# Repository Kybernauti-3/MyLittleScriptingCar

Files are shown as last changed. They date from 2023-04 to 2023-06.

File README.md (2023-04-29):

# MyLittleScriptingCar
This is my little scripting car (Maybe autonomous in the future)

## Sources

These are the components (and their 3D models) I'm going to use in this projekt:
| Part | Component | Store page | 3D model |
| --- | --- | --- | --- |
| Brain (CPU) | Raspberry pi zero 2 w | [RPishop - Zero 2 w](https://rpishop.cz/zero/4311-raspberry-pi-zero-2-w-5056561800004.html) | [GrabCAD - Zero 2 w](https://grabcad.com/library/raspberry-pi-zero-2-w-1) |
| Camera | Raspberry Pi NoIR kamera V2 | [RPishop - NoIR v2](https://rpishop.cz/mipi-kamerove-moduly/331-raspberry-pi-noir-kamera-modul-v2.html) | [Thingiverse - Rpi Camera v2.1](https://www.thingiverse.com/thing:2376448/files) |
| Stepper motors + drivers | 2x 28BYJ-48 + ULN2003 | [Techfun - 28BYJ-48 + ULN2003](https://techfun.sk/produkt/krokovy-motor-28byj-48-modul-uln2003/)| [GrabCAD - 28BYJ-48 + ULN2003](https://grabcad.com/library/28byj-48-stepper-motor-and-uln2003-stepper-motor-driver-board-1) |
| Servo (180°) | Tower Pro 180° MG90S | [LaskaKit - Tower Pro MG90S](https://www.laskakit.cz/mini-servo-mg90s-s-kovovymi-prevody/) | [Thingiverse - MG90S Tower Pro](https://www.thingiverse.com/thing:253557/files) |
| Ultrasonic sensor | HY-SRF05 US sensor | [Dratek - HY-SRF05](https://dratek.cz/arduino/1735-meric-vzdalenosti-ultrazvukovy-5pin-hy-srf05-pro-arduino.html) | [Thingiverse - HY-SRF05](https://www.thingiverse.com/thing:2403007) |
| Main board (Arduino) | Arduino Nano (china clone) | [LaskaKit - Robotdyn Nano V3](https://www.laskakit.cz/robotdyn-arduino-nano-r3--atmega328p--pripajene-piny/) | [GrabCAD - Arduino nano](https://grabcad.com/library/arduino-nano-ch340-2) <br> _Not exactly the one I used..._ |
| Arduino terminal shield | Arduino Nano Terminal | [Techfun - Nano terminal](https://techfun.sk/produkt/arduino-nano-terminal-shield/) | [GrabCAD - Nano Terminal](https://grabcad.com/library/arduino-nano-expansion-board-1) |
| Logic converter | Bi-directional logic converter | [Techfun - I2C logic converter](https://techfun.sk/cs/produkt/i2c-logick%C3%BD-konverter-5v-3-3v-4-kan%C3%A1lov%C3%BD/) | [GrabCAD - logic converter](https://grabcad.com/library/logic-level-converter-5v-to-3-3v-module-1) |
| Charger + Potection | TP4056 Micro USB | [Dratek - TP4056 Micro USB](https://dratek.cz/arduino/971-micro-usb-nabijecka-baterii.html) | [GrabCAD - TP4056 Micro USB](https://grabcad.com/library/tp4056-cargador-de-baterias-litio-lipo-5v-1a-1) |
| Battery holder | 18650 Li-Ion Holder | [Techfun - 18650 Holder](https://techfun.sk/cs/produkt/drz%C3%A1k-pro-jednu-18650-li-ion-baterii/) | [GrabCAD - 18650 Holder](https://grabcad.com/library/18650-battery-holder-generic-1) |
| Step-up converter | M 407 s MT3608 | [RadioKus - M 407](https://www.radiokus.cz/m-407-napajeci-modul-step-up-menic-2a-s-mt3608) | []() |
| Battery | 18650 Li-Ion 2800mAh 10A | [Techfun - 18650 2800mAh](https://techfun.sk/cs/produkt/18650-baterie-tenpower-inr18650-22he-2800mah-10a/) | []() |

TODO:

- [x] Gather all sources
- [x] Design chassis
- [x] Print and ready the chassis
- [x] Complete the hardware
- [x] Write the software
- [ ] Write the framework
- [ ] Add some use for the camera
- [ ] Finalize
- [ ] Play with it :)

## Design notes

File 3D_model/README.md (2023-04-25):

# 3D model for the car

This is a folder with images of all 3D models.

The parts were made (and are stored) in
[onShape](https://www.onshape.com/en/).

-----------------------------------------------------------

## Latest update:

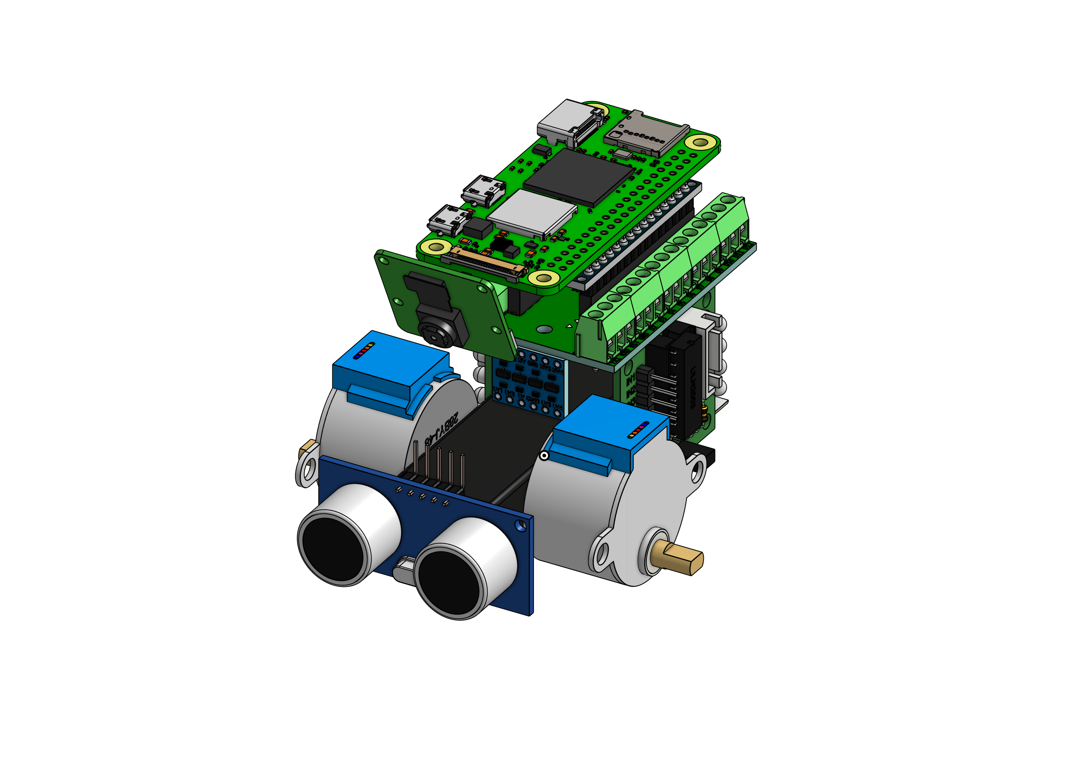
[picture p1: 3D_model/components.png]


Imported all the current parts. This is a visualization of how the parts will be placed in the final case.

> Actually made it completely different...

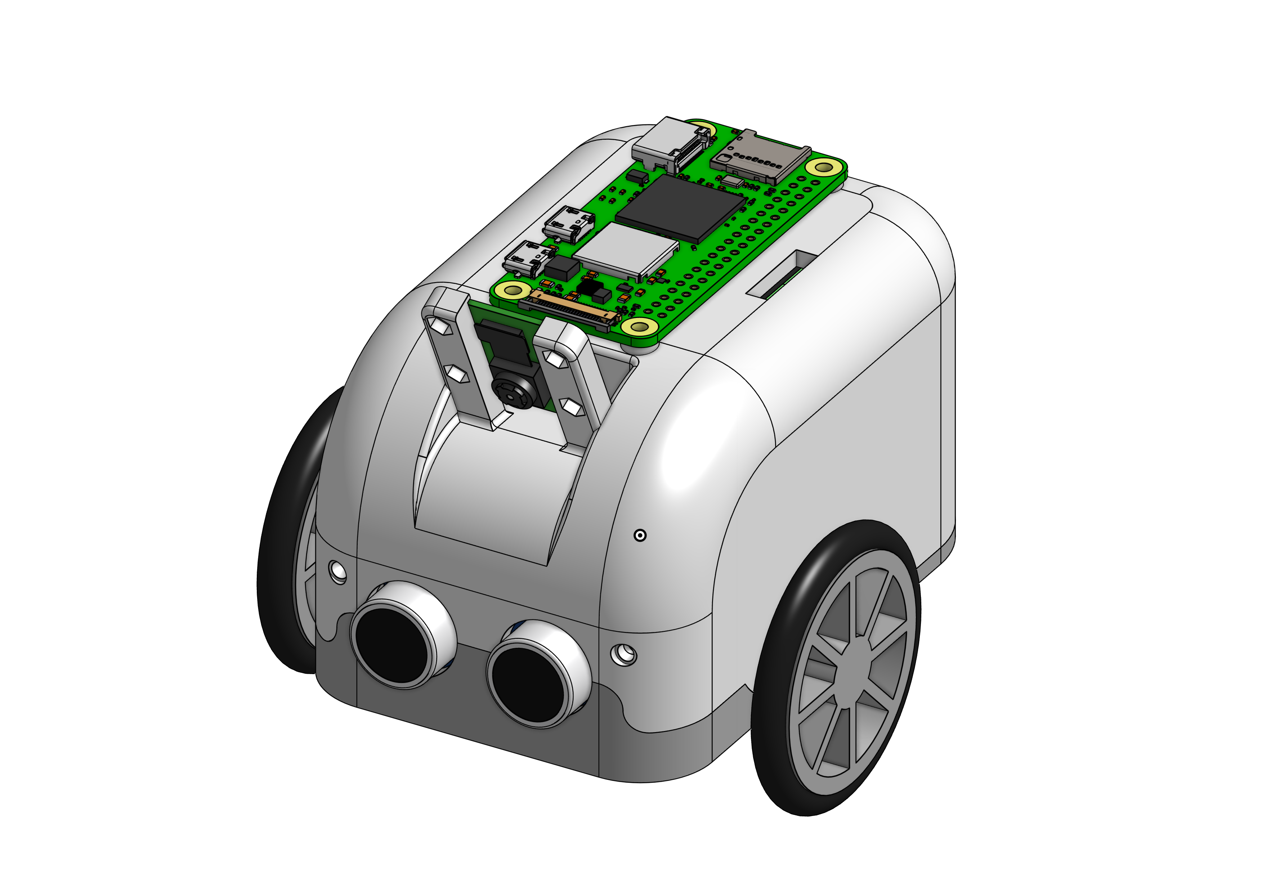
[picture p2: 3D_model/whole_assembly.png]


This is the whole assembly: All components + created parts

-----------------------------------------------------------

*The whole model can be found on the onShape cloud: [MyLittleScriptingCar](https://cad.onshape.com/documents/853826ab736a7e89ca60314d/w/e4e5486c53d8f1f4ba14f67f/e/c2fb18a20a1dab14190ffd40)*

*The model is also under HUGE development and I just don't want to spend that much time just exporting and copying files.*

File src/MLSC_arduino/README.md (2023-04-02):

# MyLittleScriptingCar _– Arduino part_

This is part of my project, that is dedicated to arduino.
For now, it contains [main.cpp](./src/main.cpp) and my custom library for controlling stepper motors – [EightStepMotor](./lib/EightStepMotor/)

In the future, this will contain all the code, that will be uploaded on the arduino, which means UART comunication, Ultrasonic senzor and maybe IMU and servo, but I'll might leave those out...

Also, there's a dependency in [platformio.ini](./platformio.ini) on Arduino Stepper library, but I used that library just as a reference, so it will get deleted later.

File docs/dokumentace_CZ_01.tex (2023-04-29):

\documentclass[12pt]{article}
\usepackage{blindtext}
\usepackage{geometry}
\geometry{
	a4paper,
	left=40mm,
	right=15mm,
	top=30mm,
	bottom=35mm,
 }
\usepackage{setspace}
% Seznam balíků
\usepackage{comment}
\usepackage{lmodern}
\usepackage{cmap}
\usepackage[czech]{babel}
\usepackage[T1]{fontenc}
\usepackage[utf8]{inputenc}
\usepackage{graphicx}
\usepackage{epstopdf}
\usepackage{makeidx}
\usepackage{listings}
\usepackage[export]{adjustbox}
\usepackage[font=scriptsize,labelfont=bf]{caption}
\usepackage{booktabs}
\usepackage{subcaption}
\usepackage{array}
\usepackage{multirow}
\usepackage{tabularray}
\usepackage{enumitem}
\usepackage{tocbibind}
\usepackage{courier}
\usepackage{pdfpages}
\usepackage{float}
\usepackage{hyperref}
\hypersetup{
	colorlinks,
	citecolor=black,
	filecolor=black,
	linkcolor=black,
	urlcolor=black
}
\usepackage{times}
\graphicspath{{./images/}}

% Začátek dokumentu
\begin{document}
	% Titulní stránka
	\begin{titlepage}
		\centering
		\fontfamily{lmss}\selectfont
		\begin{tabular}{m{0.2\linewidth}m{0.8\linewidth}}
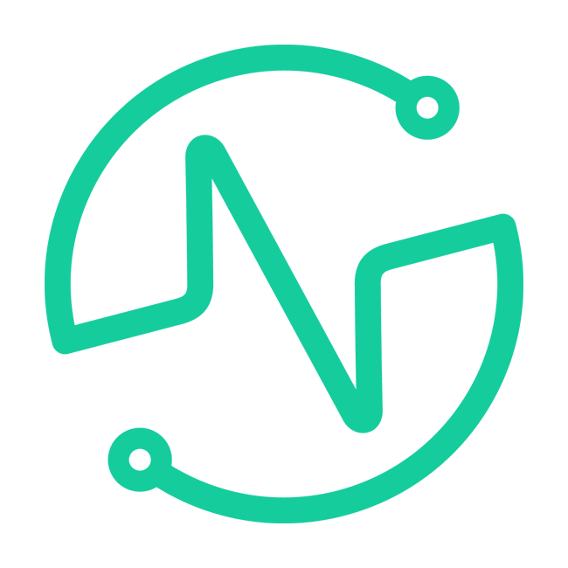
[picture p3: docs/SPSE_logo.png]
			
			&\centering
			\textbf{Vyšší odborná škola}\par
			\textbf{a Střední průmyslová škola elektrotechnická}\par
			\textbf{Plzeň, Koterovská 85}
		\end{tabular}
		\centering
		\vfill
		{\Huge\sc\textsf{\textbf{Ročníková práce}}\par}
		\raggedright
		\vspace{4cm}
		{\Large Téma: \textbf{Programovatelné auto}\par}
		\vfill
		
		% Spodní část titulní stránky
		\textbf{\begin{tabular}{ll}
			Autor práce:		&	Jan Ocelík \\
			Obor studia:		&	78-42-M/01 Technické lyceum \\
			Třída:				&	3. L \\
			Předmět:			&	Kybernetika \\
			Zadávající učitel:	&	Jiří Švihla \\
			Dne:				&	28. 4. 2023 \\
								&	\\
			Hodnocení:			&	\\
		\end{tabular}}
	\end{titlepage}

	% Zadání
	\thispagestyle{empty}
	\includepdfset{offset=15mm 0mm,noautoscale,pages={-},pagecommand={}}
	\includepdf[pages=1]{Zadani_RP_TL_22_23.pdf}
	
	\begin{spacing}{1.5}
	
	% Anotace
	\newpage
	\thispagestyle{empty}
	\section*{Anotace}
	\addcontentsline{toc}{section}{Anotace}
	\paragraph{} Cílem této ročníkové práce je za pomoci opensource programů navrhnout a z opensource komponent poskládat robotické autíčko pro začátečníky i pokročilé s možností jednoduchého sestavení. Dalším úkolem je vyvinout firmware a API pro jednoduché skriptové programovaní i komplexnější programování s využitím obrazového vstupu. Dalším úkolem je připravit ukázkové příklady kódu k předvedení jednotlivých funkcí robota. Posledním úkolem je zpříjemnit práci s robotem, zhodnotit přínosy a možnosti využití projektu ve vzdělávání a vypracovat potřebnou dokumentaci.
	\vfill
	\paragraph{} „Prohlašuji, že jsem tuto práci vypracoval samostatně a použil literárních pramenů a informací, které cituji a uvádím v seznamu použité literatury a zdrojů informací.“
	\paragraph{} „Souhlasím s využitím mé práce učiteli VOŠ a SPŠE Plzeň k výuce.“
	\paragraph{} \hfill Plzni dne: .................... Podpis: ....................
	
	% Poděkování
	\newpage
	\thispagestyle{empty}
	\section*{Poděkování}
	\addcontentsline{toc}{section}{Poděkování}
	\paragraph{} Tímto bych chtěl poděkovat vedoucímu práce Jiřímu Švihlovi za pomoc s výběrem komponent a obsahem dokumentace a rodině a přátelům za psychickou podporu. Také děkuji všem dohromady za to, že mě k tomu včas dokopali.
	
	% Obsah
	\newpage
	\tableofcontents
	
	% Úvod
	\newpage
	\section{Úvod}
	\paragraph{} V dnešní době se stále více hovoří o automatizaci a digitalizaci a tyto trendy mají velký vliv na společnost. Robotika a autonomní systémy jsou jednou z klíčových oblastí, které se rozvíjejí v rámci těchto trendů a mají potenciál změnit mnoho aspektů našeho života.
	\paragraph{} Vzdělávání a výuka v této oblasti se také stávají stále důležitějšími, protože mnoho pracovních pozic, které budou v budoucnosti vyžadovat znalosti robotiky a programování, ještě neexistuje. Výuka v této oblasti tak může být klíčová pro přípravu studentů na pracovní trh budoucnosti.
	\paragraph{} Proto jsem se rozhodl věnovat svou ročníkovou práci právě problematice robotiky a vytvořit autonomní auto, které bude sloužit jako výuková pomůcka. Můj záměr je ukázat, jak moderní technologie mohou být využity k tomu, aby byli studenti lépe připraveni na budoucí výzvy v oblasti robotiky a informatiky.
	\paragraph{} Při tvorbě prototypu se budu snažit využít nejnovější poznatky v oblasti robotiky a programování, a to jak z teoretického hlediska, tak praktických zkušeností z mých předchozích aktivit. Cílem bude vytvořit zařízení, které bude snadno ovladatelné a srozumitelné pro studenty různých věkových kategorií, a zároveň bude dostatečně funkční a výkonné pro splnění zadaných úkolů.
	\paragraph{} Věřím, že tato ročníková práce přispěje k popularizaci robotiky a podpoří zájem studentů o tuto oblast. To může mít pozitivní vliv na jejich budoucí kariéru a na rozvoj robotiky v České republice.
	
	% Cíle a požadavky
	\newpage
	\subsection{Cíle a požadavky}
	
	\subsubsection{Komponenty (moduly)}
	\paragraph{} Hlavním cílem této ročníkové práce je návrh a výroba robota z běžně dostupných materiálů, v tomto případě ze snadno sehnatelných modulů.
	\paragraph{} Moduly by měly být zároveň opensource, aby si software pro ně mohl programovat každý, který se k robotovi dostane, nebo si ho sám vyrobí.
	\paragraph{} Důležitý je také výběr napájení, v případě robotického auta tedy baterie, tak, aby udrželo robota v provozu po přiměřeně dlouhou dobu a aby zároveň dokázalo vykrýt proudové špičky.
	
	\subsubsection{Šasi (tělo)}
	\paragraph{} Tělo robota by mělo být vyrobeno tak, aby bylo plně uzavíratelné, tedy bezpečné pro jakýkoli přenos i při nešetrném zacházení, ale aby se dal robot také provozovat s plně přístupnými veškerými propojkami a bylo tedy snadné ladit jeho software za provozu.
	
	\subsubsection{API}
	\paragraph{} Jedním z dalších požadavků je co nejvíce zpříjemnit uživateli práci s robotickým autem, tedy vytvořit nějaké API nebo knihovnu.
	\paragraph{} Nedílnou součástí je také dokumentace k danému API/knihovně a to proto, aby si i nový uživatel zvládl bez jakékoli pomoci robota pomocí daného API/knihovny naprogramovat.
	
	% Návrhový software
	\newpage
	\subsection{Návrhový software}
	
	\subsubsection{Onshape}
	\paragraph{} Onshape je online software pro návrh 3D součástí. V programu se vytváří takzvaný dokument, ve kterém se nadále dají zakládat \uv{studia}. Onshape nabízí mnoho zajímavých možností, běžného uživatele však zajímají tato tři hlavní studia - \textbf{Part Studio}, \textbf{Assembly} a \textbf{Drawing}.
	\subsubsection*{Part Studio}
	\paragraph{} Part Studio slouží, jak už název napovídá, k vytváření jednotlivých dílů. Díly se vytvářejí a upravují pomocí příkazů, jako například \textbf{Sketch} (sloužící k sestrojení 2D náčrtu), \textbf{Extrude} (\uv{vytáhnutí} náčrtu do třetího rozměru) nebo \textbf{Fillet} (zaoblení hran). Tyto příkazy lze vyvolat kliknutím na jejich ikonu v horní liště programu, přepsáním jejich názvu do \textbf{Search tools}, nebo, u některých více používaných, klávesovými zkratkami.
	
	\begin{figure}[H]
		\centering
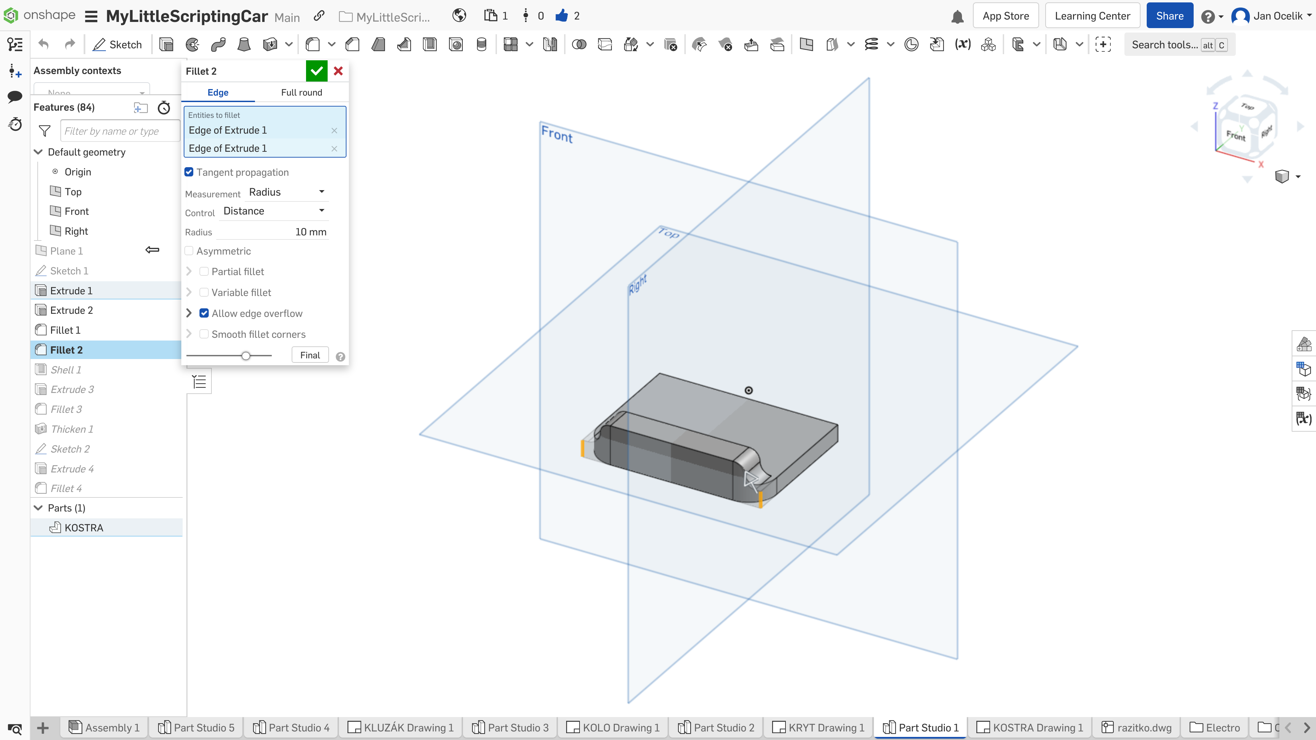
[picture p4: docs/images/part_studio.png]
		
		\caption{Part Studio}
		\label{fig:part_studio}
	\end{figure}
	
	\subsubsection*{Assembly}
	\paragraph{} Další studio v programu Onshape, Assembly, slouží ke spojování (nebo alespoň aranžování) jednotlivých dílů. K tomuto účelu slouží příkazy, které se opět nechají vyvolat několika způsoby, včetně klepnutí na ikonu v horní liště studia. Další výhodnou funkcí tohoto studia je \textbf{Create Part Studio in context}, což dělá přesně to, co se v názvu píše; vytvoří studio dílu v kontextu se sestavou. Tato funkce může hodně usnadnit vytváření některých dílů.
	
	\begin{figure}[H]
		\centering
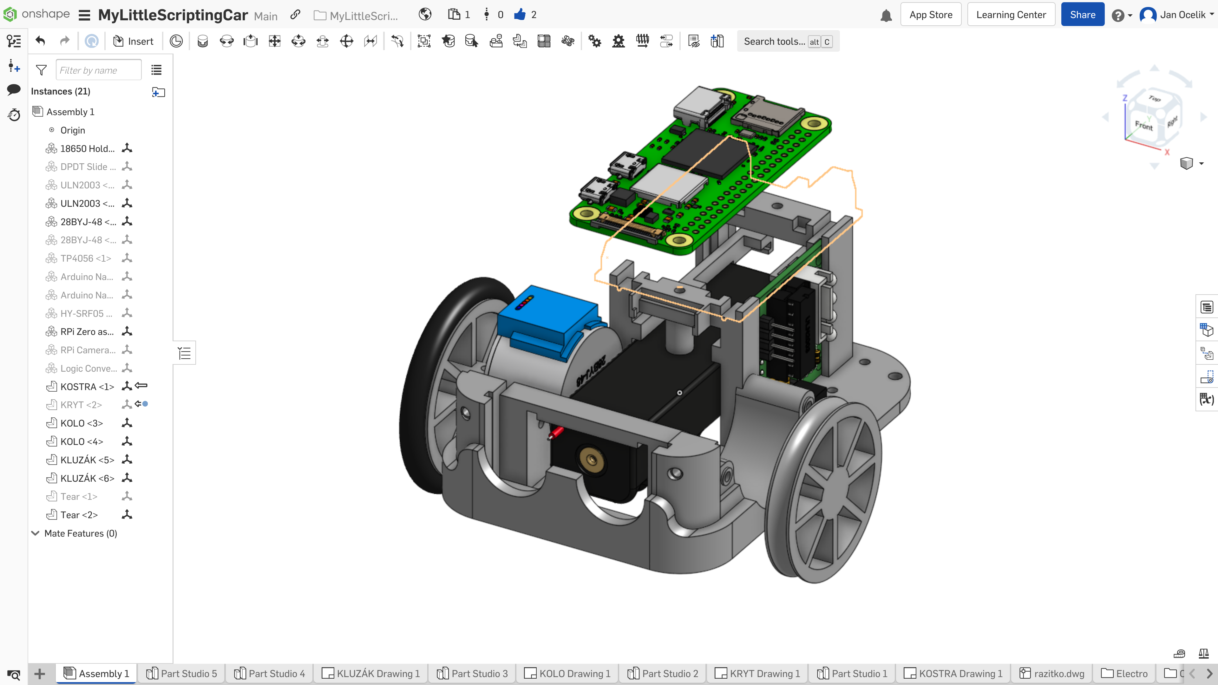
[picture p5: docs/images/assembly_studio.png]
		
		\caption{Assembly}
		\label{fig:assembly_studio}
	\end{figure}
	
	\subsubsection*{Drawing}
	\paragraph{} Drawing se dá vyvolat jak samostatně, tak rovnou v kontextu s daným dílem a to jak z Part Stuido, tak z Assembly. Uživateli stačí, když v seznamu dílů vybere danou položku a přes kontextové menu vybere možnost \textbf{Create Drawing of...}. Výkres se zde upravuje také pomocí příkazů, stejně jako v předešlých studiích. \textbf{Drawing} studio umožňuje také globální nastavení kót, písma, čar atd.
	
	\begin{figure}[H]
		\centering
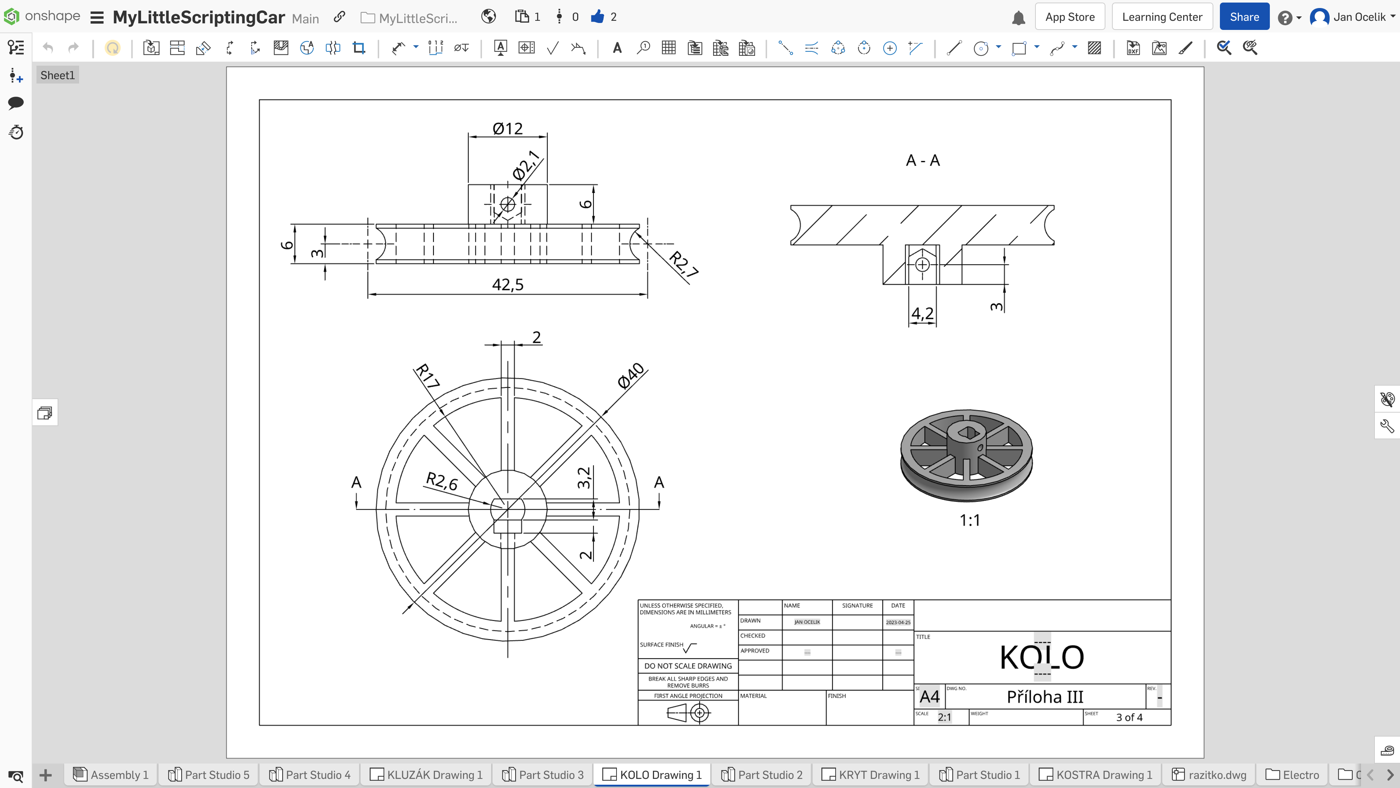
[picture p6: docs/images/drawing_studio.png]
		
		\caption{Drawing}
		\label{fig:drawing_studio}
	\end{figure}
	
	\subsubsection{Code OSS/VS Code}
	
	\begin{figure}[H]
		\centering
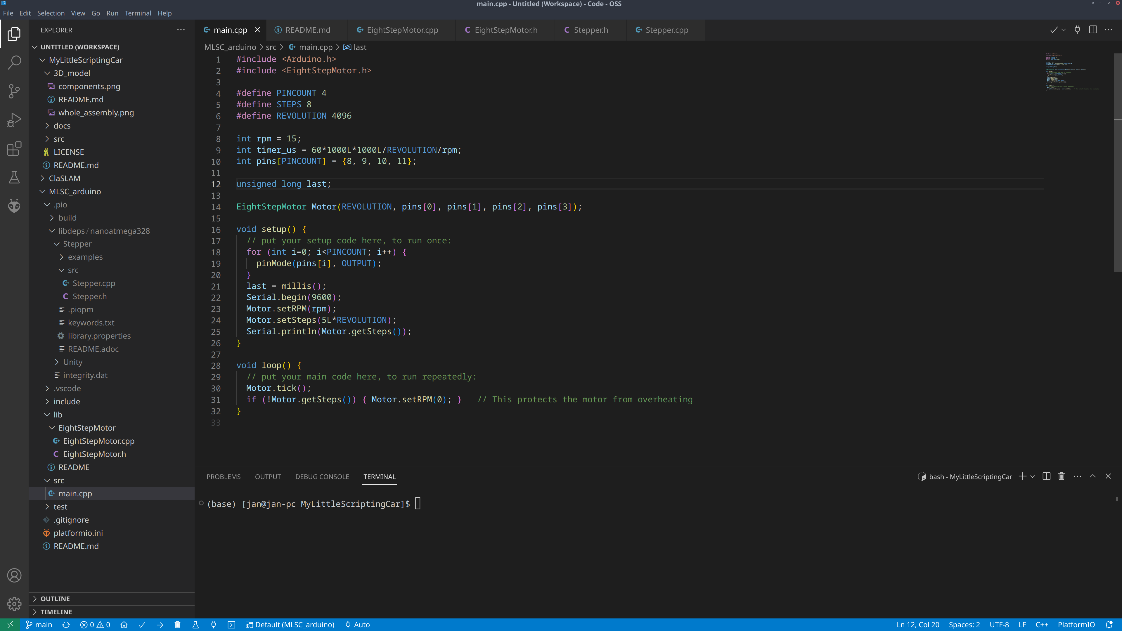
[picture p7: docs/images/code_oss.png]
		
		\caption{Code OSS}
		\label{fig:code_oss}
	\end{figure}
	
	\paragraph{} Code OSS je opensource IDE vyvíjené firmou Microsoft. Vzniklo jako konkurent programu Atom, který se nyní již nevyvíjí. Stal se oblíbeným hlavně díky podpoře obrovského množství programovacích i značkovacích jazyků (např. python, c++, java, xml, html). Má také velice intuitivní ovládání a šikovně zvolenou paletu barev.
	
	\paragraph{} Code OSS a Visual Studio Code jsou téměř identické programy, jediným pozorovatelným rozdílem je absence některých rozšíření v \uv{marketplace} v Code OSS (i to se dá ale snadno opravit).
	
	\subsubsection*{PlatformIO}
	\paragraph{} Platformio je rozšíření do VS Code umožňující překlad C++ kódu a následný upload do předdefinovaných jednočipů (např. atmega328). Je to šikovný kus softwaru s několika užitečnými funkcemi navíc, jako např. automatická detekce zařízení, seznam dostupných knihoven, snadná instalace a integrace daných knihoven do projeků a další.
	
	\begin{figure}[H]
		\centering
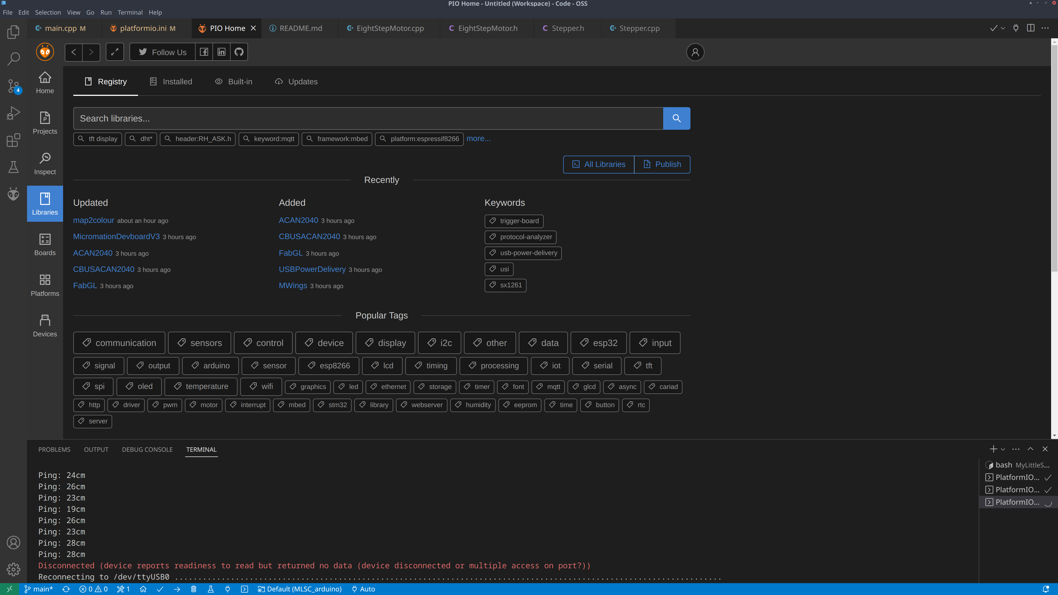
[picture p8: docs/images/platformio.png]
		
		\caption{PlatformIO}
		\label{fig:platformio}
	\end{figure}
	
	% Výrobní technologie
	\newpage
	\subsection{Výrobní technologie}
	\subsubsection{3D tisk}
	\paragraph{} 3D tisk je moderní technologie, která umožňuje vytvářet fyzické objekty ze 3D digitálních modelů. Tento proces začíná vytvořením digitálního modelu pomocí počítačového softwaru. Poté je tento digitální model převeden do formátu, který je kompatibilní s 3D tiskárnou. V~průběhu tiskového procesu se materiál, obvykle termoplastického typu, zahřívá a aplikuje na specifická místa v souladu s digitálním modelem. Tento postup se opakuje vrstva po vrstvě, dokud není celý objekt hotov.
	
	\paragraph{} 3D tisk má mnoho výhod, například umožňuje rychlé prototypování a výrobu malých sérií komplexních geometrických objektů. To se stává velmi užitečné v oblasti průmyslové výroby, kde může být vytvoření prototypu značně nákladné a časově náročné. Díky 3D tisku se náklady na výrobu mohou snížit a doba výroby může být zkrácena.
	
	\paragraph{} V posledních letech se cena 3D tiskáren snížila a uživatelé si mohou tisknout vlastní návrhy přímo z domova. Tato technologie také umožňuje vytvářet přizpůsobené a jedinečné předměty, což je velmi užitečné pro řadu různých aplikací, včetně medicíny, průmyslu a uměleckých oborů.
	
	\paragraph{} Díky jednoduchosti použití a možnosti tvorby téměř jakýchkoli tvarů je ideální volbou k~výrobě kostry programovatelného auta.
	
	\begin{figure}[H]
		\centering
		
		\caption{Vytištěný model kostry, kol a kluzáků auta (vlevo) -- Tisk modelu krytu (vpravo)}
		\label{fig:tisk_kostra_kryt}
	\end{figure}

	% Vybrané komponenty (moduly)
	\newpage
	\section{Popis konstrukce a vybrané moduly}
	\subsection{Vybrané moduly}
	
	\paragraph{} Pro ovládání motorů bylo nutné vybrat \uv{řídící jednotku}. Pro tento účel se nejen kvůli rozměrům jevila jako jasná volba Arduino Nano, ale kvůli ceně bylo lepší sáhnout po dostupnějším klonu: \textbf{\textit{Robotdyn Arduino Nano V3}}.
	Piny na Arduinu jsou přístupné pouze ze spodní strany desky, což je vzhledem k jeho umístění v robotovi dosti nešikovné. Elegantním řešením problému je takzvaný terminál, který piny zpřístupní z boků.
	
	\paragraph{} Kvůli předpokládanému univerzálnímu využití robota bylo nutné zvolit také vhodný pohon. Tím se ukázaly být krokové motory. K motorům jsou potřeba také řadiče a to kvůli velkým proudům, které mohou motory procházet.
	Aby mohl být robot alespoň částečně autonomní, je téměř nutností přidat nějaké vstupní periferie, které poslouží k získávání zpětné vazby k řízení, jako například: \textbf{\textit{Ultrazvukový měřič vzdálenosti HY-SRF05}}.
	
	\paragraph{} Pro správné fungování robota bylo nutné zvolit vhodné napájení. U autonomního zařízení je jasnou volbou nabíjecí baterie a díky své popularitě a rozšíření je nejlepší možností \textbf{\textit{Li-ion baterie 18650}} v kombinaci s dobíjecím modulem \textbf{\textit{M 401A}} a step-up měničem \textbf{\textit{M 407}}.
	Na baterii je také nutné vybrat vhodný držák a vzhledem k jejímu umístění je potřeba zvolit takový, který baterii udrží ve správné pozici i při hrubším zacházení s robotem.
	Je také nutné mít možnost robota nějak vypnout/odpojit (přerušit obvod), v ideálním případě napájecí obvod kompletně izolovat. Proto je dobré zvolit dvoucestný přepínač, například \textit{\textbf{posuvný dvojitý přepínač}}.
	
	\paragraph{} \textbf{\textit{Raspberry Pi Zero 2 w}} je vhodným modulem pro rozšíření funkcí robota, který se propojí s Arduinem (řídícím modulem) pomocí asynchronní sériové linky a umožní tak rychlejší zpracování údajů získaných z dalších rozšiřujících modulů, například z \textbf{\textit{Raspberry Pi Camera 2 NoIR}}. Protože Raspberry a Arduino pracují na různých hladinách napětí, je potřeba pro bezpečné propojení a komunikaci mezi těmito moduly použít \textit{\textbf{převodník logických hodnot}}.
	
	\begin{figure}[H]
		\centering
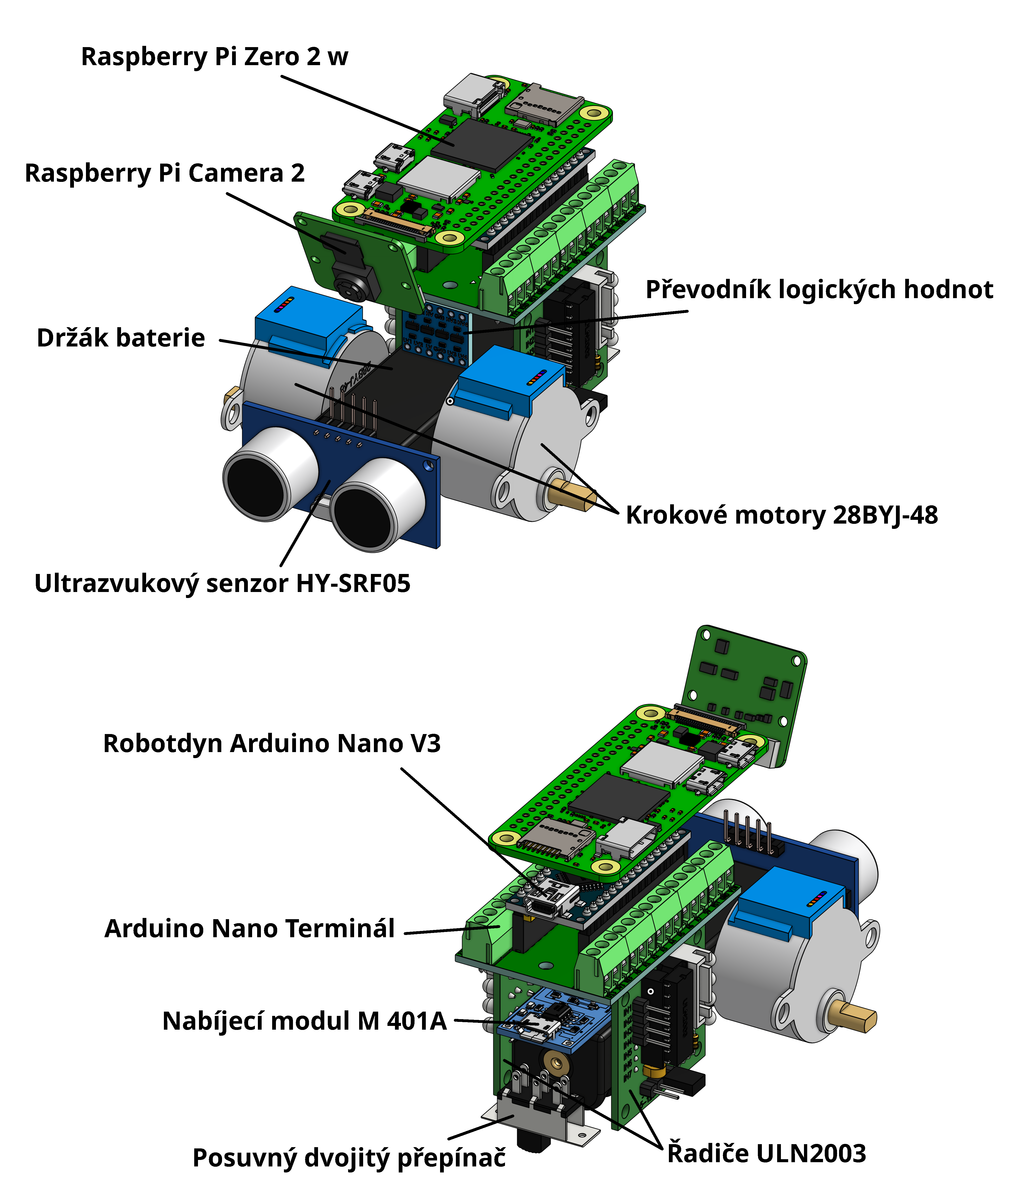
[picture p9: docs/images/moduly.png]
		
		\caption{Umístění modulů v robotovi}
		\label{fig:moduly}
	\end{figure}
	\newpage	
	\subsection{Konstrukce}
	\paragraph{} Cílem této práce bylo navrhnout kostru programovatelného auta tak, aby bylo co nejkompaktnější a zároveň aby se zachovala snadná přístupnost ke všem integrovaným modulům.
	
	Kostra je navržena tak, aby většina modulů mohla být nainstalována pouhým zasunutím do drážek a pomocí gravitace, zacvaknutím, nebo překrytím jiným modulem. Díky tomu bylo použito co nejméně šroubových spojů.
	
	Krokové motory bylo třeba pevně ukotvit usazením do výřezů, které kopíruje tvar jejich těl, a zajištěním samořeznými šrouby.
	
	Ultrazvukový senzor je zasunut do drážky, která jej těsně obklopuje ze tří stran. Zamezí se tím nežádoucím vibracím senzoru při pohybu robota.
	
	Držák baterie je kvůli usnadnění výměny baterie umístěn na spodní straně tak, aby baterie byla přístupná bez nutnosti odstraňovat kryt robota. Napájecí obvod, včetně nabíjecího modulu, je snadno přístupný a může tak být v případě potřeby bez problémů vymontován.
	
	Vypínač je umístěn na spodní straně vzadu a ke kostře pevné uchycen samořeznými šrouby, kvůli předpokládanému častému používání.
	
	Arduino je umístěno tak, aby byl snadno přístupný jeho programovací konektor. Pomocí terminálu, do nějž je Arduino zasunuto, byly zpřístupněny všechny jeho piny (svorky). Samotný terminál je ukotven ke kostře samořeznými šrouby.
	
	Vzhledem k vysoké kompaktnosti robota byly použity pouze dva krokové motory, tedy navržené auto má pouze dvě kola. Pro zajištění stability auta je nutné mít alespoň tři opěrné body (zde dvě kola a jeden kluzák). Kvůli umístění vypínače uprostřed robota bylo nutné zvýšit počet dodatečných opěrných bodů (kluzáků) na dva a umístit je po stranách vypínače.
	
	Aby se zabránilo prokluzování kol na osách krokových motorů, jsou navržená kola vybavena integrovanou matičkou a šroubkem M2, které pomocí tření zabrání sklouznutí kola z osy.
	
	Pro zvýšení přilnavosti kol k podkladu při pohybu robota byla použita toroidová těsnění (průměr 42mm/5,5mm) jako pneumatiky, která jsou usazena v drážce na kolech.
	
	Základ robota obsahuje pouze Arduino a moduly, které zajišťují základní funkce: pohyb, napájení a sběr dat ze vstupní periferie (ultrazvukového senzoru).
	
	\begin{figure}[H]
		\centering
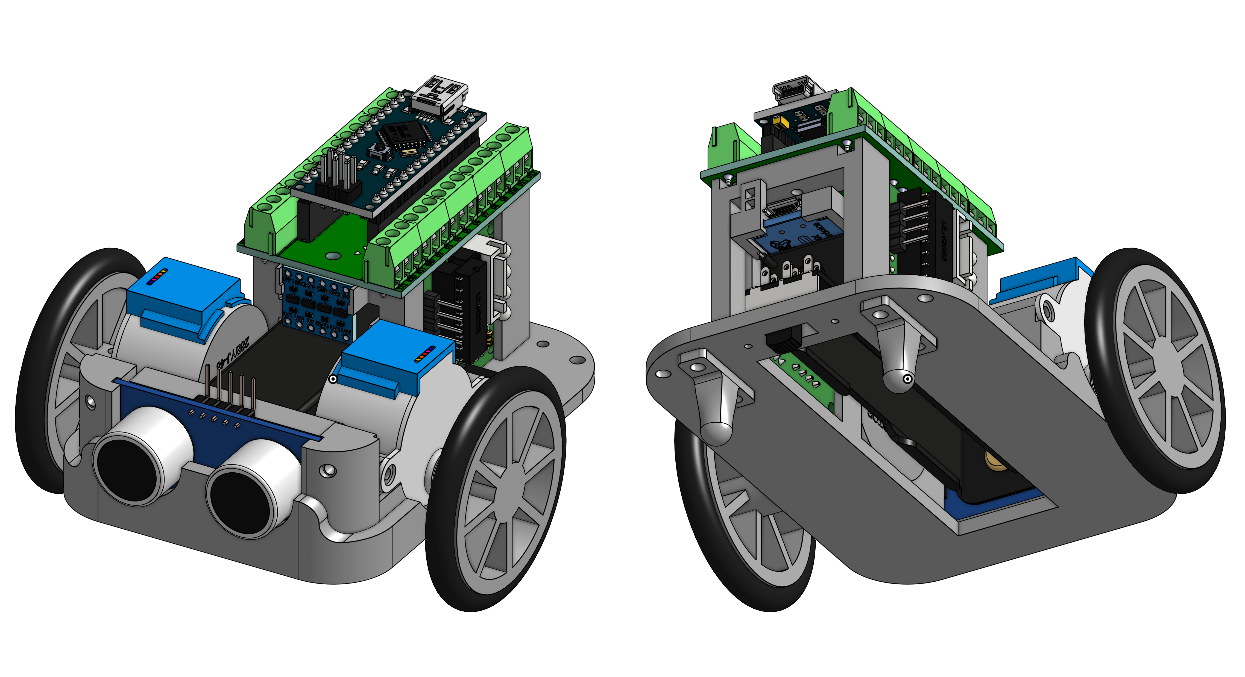
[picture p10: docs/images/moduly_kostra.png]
		
		\caption{Umístění modulů na kostře auta}
		\label{fig:moduly_kostra}
	\end{figure}
	
	Na zádech robota je provizorně umístěna kamera a Raspberry Pi, které slouží v této práci pouze k demonstraci řízení robota posíláním příkazů přes sériovou linku Arduinu a pomocí dat získaných z ultrazvukového senzoru a kamery připojené přímo do Raspberry Pi. Tímto propojením se, obrazně řečeno, z Arduina stává \uv{mícha}, která předává příkazy z \uv{mozku} (Raspberry Pi) do periferií.
	
	\begin{figure}[H]
		\centering
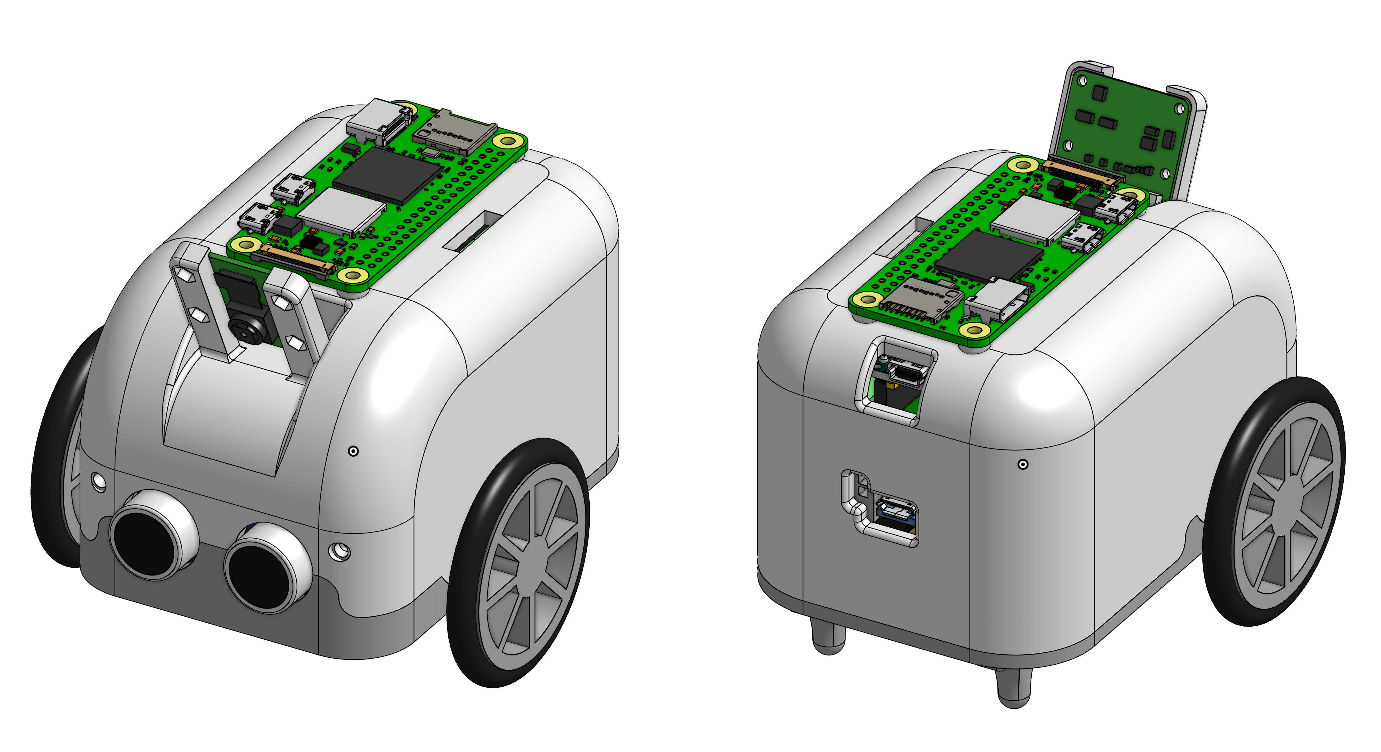
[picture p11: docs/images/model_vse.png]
		
		\caption{Zakrytované auto s rozšiřujícími moduly (Raspberry Pi)}
		\label{fig:model_vse}
	\end{figure}
	
	% Software
	\newpage
	\section{Software}
	
	\paragraph{}Hlavní činností Arduina je nízkoúrovňová správa základního hardwarového vybavení robota, tedy krokových motorů a ultrazvukového senzoru.
	
	Pro řízení krokových motorů existuje několik knihoven, avšak žádná z nich nesplňovala požadavky na paralelizaci s ostatními procesy. Z tohoto důvodu jsem vytvořil vlastní knihovnu využívající možnosti paralelního ovládání motorů na základě zadané rychlosti a počtu kroků. Využil jsem objektově orientovaného přístupu a každý motor je tak nezávislou instancí společné třídy.
	
	Podobný přístup využívá i opensource knihovna NewPing pro měření vzdálenosti od překážky ultrazvukovým senzorem. 
	
	Pro komunikaci mezi Arduinem a nedřízeným systémem, např. Raspberry Pi nebo PC, jsem si navrhl jednoduchý komunikační protokol umožňující snadné a intuitivní ovládání motorů a měření vzdálenosti od překážky (viz tabulka níže).
	
	\begin{figure}[H]
		\begin{spacing}{1}
			\begin{tabular}{|c|c|c|c|}
				\hline
				\textbf{g}			&	\textbf{r}		&	\textbf{v}		& \\
				získat hodnotu		&	pravý motor		&	rychlost (rpm)	& \\
									&	\textbf{l}		&	\textbf{n}		& \\
									&	levý motor		&	počet kroků		& \\
				&&&\\
									&	\textbf{u}		&					& \\
									&	ultrazvukový senzor &				& \\
				\hline
				\textbf{s}			&	\textbf{r}		&	\textbf{v}		& \textbf{\textpm000}\\
				nastavit hodnotu	&	pravý motor		&	rychlost (rpm)	& hodnota (-150 až +150)\\
									&	\textbf{l}		&	\textbf{n}		& \textbf{0000}\\
									&	levý motor		&	počet kroků		& hodnota (0 až 9999)\\
				&&&\\
									&	\textbf{u}		&	\textbf{0}		& \\
									&	ultrazvukový senzor & zapnuto/vypnuto & \\
				\hline
			\end{tabular}
		\end{spacing}
	\end{figure}
	
	Například:\par
	\textbf{"srv+149"} -- Arduino nastaví rychlost pravého motoru na 14,9 rpm (otáček za minutu).\par
	\textbf{"gu"} -- Arduino vrátí hodnotu získanou z ultrazvukového senzoru.

	V případě žádosti o získání hodnoty vrátí Arduino po sériové lince požadovanou hodnotu jen jako číslo.
	
	%Závěr
	\newpage
	\section{Závěr}
	\paragraph{} 
	
	Téma této ročníkové práce jsem si zvolil na základě předchozích praktických zkušeností s návrhem vlastních robotů. Pro první konstrukce jsem používal na laserové gravírce vyřezávanou překližku a později mi rozšíření a zlevnění 3D tisku umožnilo používat i tyto moderní technologie. 
	Kostru, kryt, kola a kluzáky tohoto robota jsem vytiskl na 3D tiskárnách na VOŠ a SPŠE Plzeň.
	
	Arduino, ultrazvukový senzor, Raspberry Pi Zero 2 w a kamera jsou z mých vlastních zásob, ostatní moduly/součásti pro napájení a pohon jsem zakoupil přímo pro tento projekt na webu https://techfun.sk, https://radiokus.cz a https://dratek.cz.
	
	Krokové motory by se mohli zdát jako nevhodně zvolené pro jejich pomalost, ale zvolil jsem je z důvodu jejich robustnosti a odolnosti, protože pro použití ve výuce není rychlost rozhodující.
	
	Pro krátkodobé použití s možností baterii kdykoli dobít je jedna baterie zcela postačující a robot tak může být kompaktnější.
	
	Po praktických zkušenostech s návrhem této verze programovatelného auta bych do budoucna uvažoval o vlastním návrhu plošného spoje integrujícího funkce většiny použitých modulů. V tomto návrhu jsem také podcenil velikost potřebného prostoru pro vedení kabelů. Kryt je tedy velice těsný a při častější manipulaci hrozí poškození některých kabelů.
	
	V této fázi Raspberry Pi s kamerou není plně integrován do robota a slouží pouze k demonstraci možností komunikace s robotem a v příštím návrhu bych jej chtěl pojmout jako rozšiřitelný kapotovaný modul pro větší odolnost.
	
	Přínosem této ročníkové práce pro mě byly hlavně nové zkušenosti s návrhem šasi v https://onshape.com a tvorbou vlastní knihovny pro ovládání krokových motorů.
	
	Také jsem si uvědomil, jak je důležité si práce na projektu rozvrhnout s dostatečným časovým předstihem a snažit se je dodržet.
	
	\begin{figure}[H]
		\centering
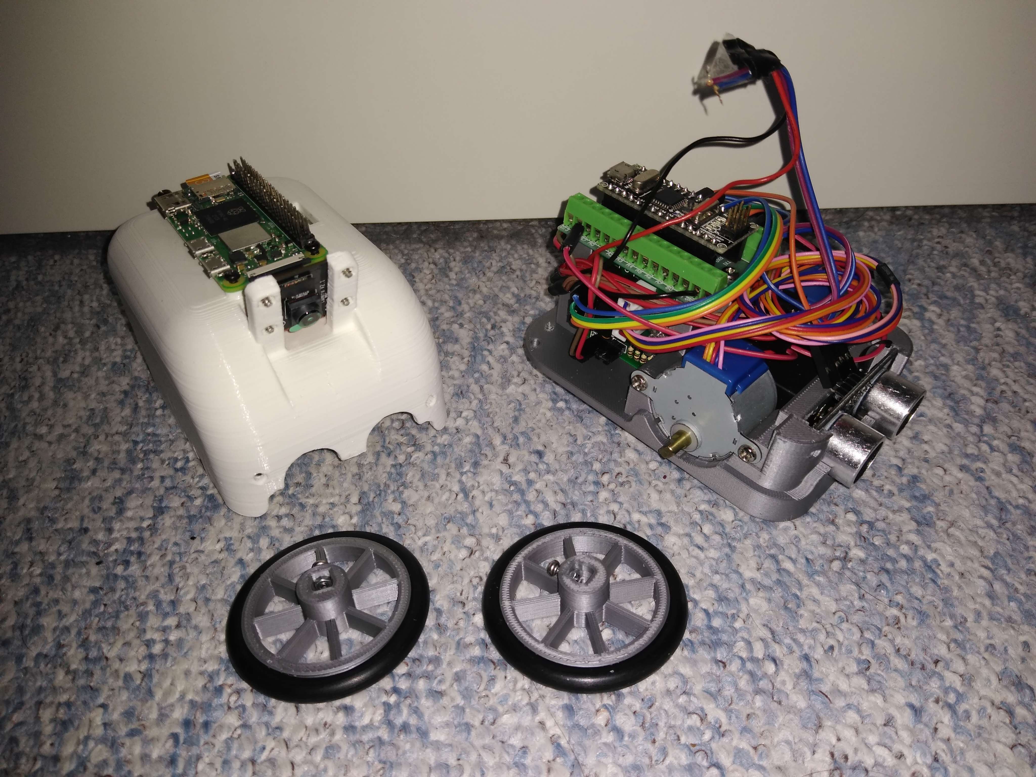
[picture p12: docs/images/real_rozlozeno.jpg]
		
		\caption{Foto rozloženého auta}
		\label{fig:real_rozlozeno}
	\end{figure}
	\begin{figure}[H]
		\centering
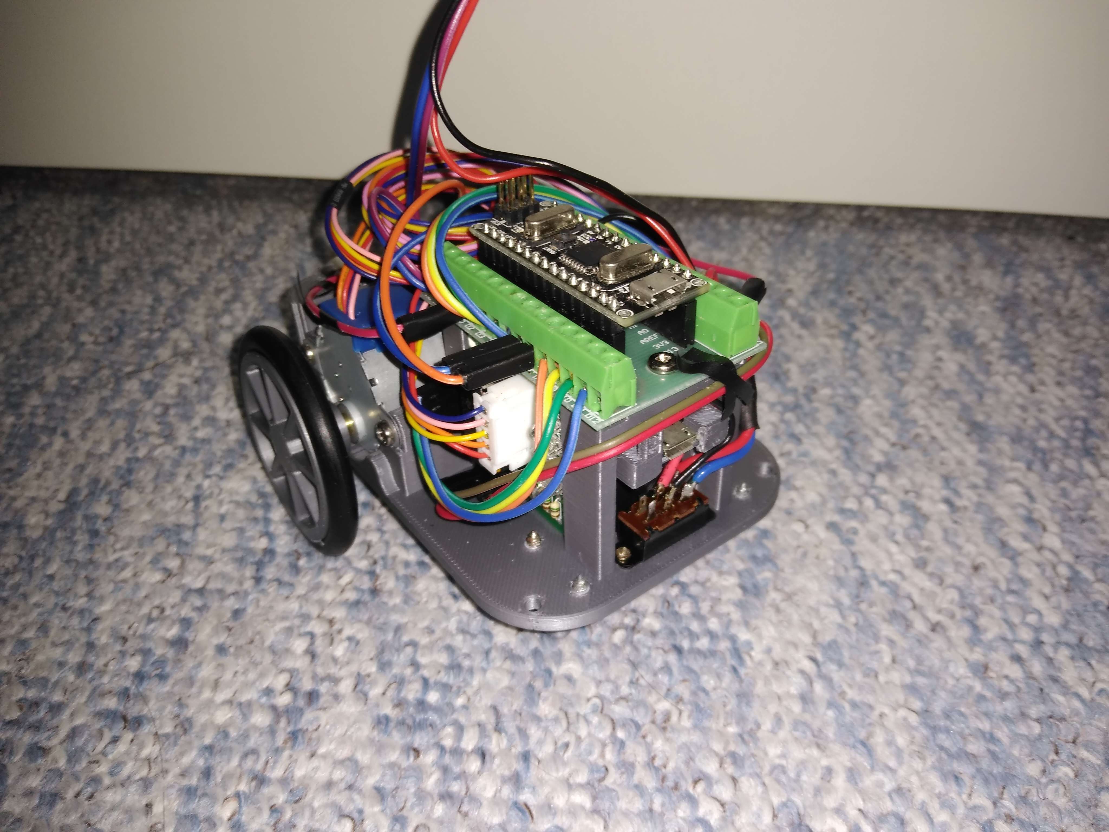
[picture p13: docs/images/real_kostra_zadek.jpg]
		
		\caption{Foto kostry auta zezadu}
		\label{fig:real_kostra_zadek}
	\end{figure}
	\begin{figure}[H]
		\centering
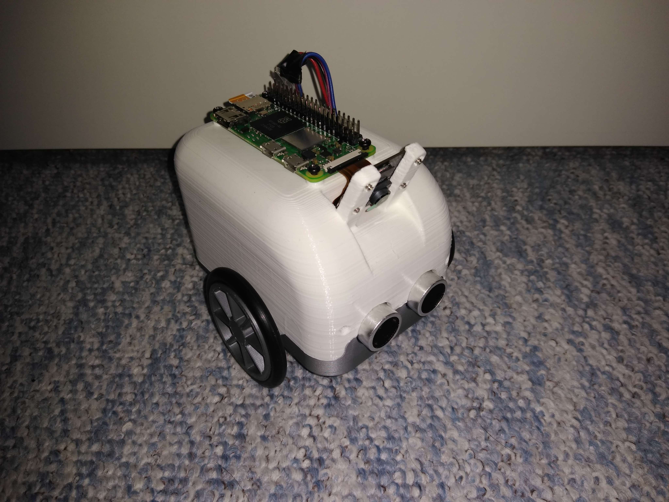
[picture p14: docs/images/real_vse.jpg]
		
		\caption{Foto složeného auta}
		\label{fig:real_vse}
	\end{figure}
	
	%Seznam obrázků
	\newpage
	\listoffigures
	
	%
	\newpage
	\section*{Seznam příloh}
	\addcontentsline{toc}{section}{Seznam příloh}
	\begin{spacing}{1}
		\paragraph{} Příloha I.: KOSTRA - výkres	
		\paragraph{} Příloha II.: KRYT - výkres	
		\paragraph{} Příloha III.: KOLO - výkres	
		\paragraph{} Příloha IV.: KLUZÁK - výkres	
		\paragraph{} Příloha V.: Schéma zapojení - výkres
		\paragraph{} Příloha VI.: Kód projektu - MLSC\_arduino.zip (elektronicky)
		\paragraph{} Příloha VII.: 28byj-48\_uln2003\_datasheet.pdf (elektronicky)
		\paragraph{} Příloha VIII.: BSS138.pdf (elektronicky)
		\paragraph{} Příloha IX.: camera-module-2-mechanical-drawing.pdf (elektronicky)
		\paragraph{} Příloha X.: camera-module-2-schematics.pdf (elektronicky)
		\paragraph{} Příloha XI.: Gravitech\_Arduino\_Nano3\_0.pdf (elektronicky)
		\paragraph{} Příloha XII.: HY-SRF05-ETC.pdf (elektronicky)
		\paragraph{} Příloha XIII.: Logic\_Level\_Bidirectional.pdf (elektronicky)
		\paragraph{} Příloha XIV.: MT3608.pdf (elektronicky)
		\paragraph{} Příloha XV.: raspberry-pi-zero-2-w-productbrief.pdf (elektronicky)
		\paragraph{} Příloha XVI.: raspberry-pi-zero-2-w-reduced-schematics.pdf (elektronicky)
		\paragraph{} Příloha XVII.: TP4056-micro-usb.pdf (elektronicky)
	\end{spacing}

\end{spacing}

\end{document}
% Konec dokumentu

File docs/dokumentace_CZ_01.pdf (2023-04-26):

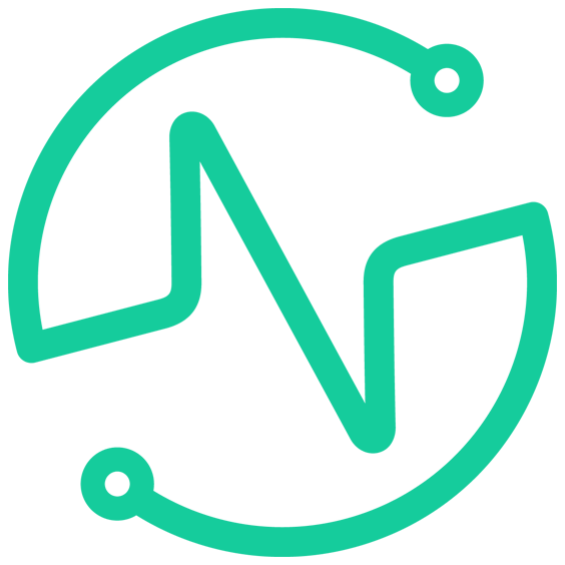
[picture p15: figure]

Vyšší odborná škola
a Střední průmyslová škola elektrotechnická Plzeň, Koterovská 85

### Ročníková práce

## Téma: Programovatelné auto

Autor práce: | Jan Ocelík
Obor studia: | 78-42-M/01 Technické lyceum
Třída: | 3. L
Předmět: | Kybernetika
Zadávající učitel: Jiří Švihla
Dne: | 28. 4. 2023

Hodnocení:

Vyšší odborná škola a

Střední průmyslová škola elektrotechnická

Plzeň, Koterovská 85

Z A D Á N Í | R O Č N Í K O V É P R Á C E
Školní rok | 2022/ 2023
Studijní obor | 78-42-M/01 Technické lyceum
Jméno a příjmení | Jan Ocelík
Třída | 3.L
Předmět | Kybernetika
Hodnoceno v předmětu | Kybernetika
Téma | Programovatelné auto
Obsah práce | 1. Sehnání součástek 2. Design a tisk modelu (šasi auta) 3. Sestavení prototypu 4. Vytvoření Framework/SDK/API 5. Naprogramování
Zadávající učitel Příjmení, jméno | Švihla Jiří

Podpis zadávajícího učitele

Termín odevzdání | 28. dubna 2023
V Plzni dne: 30. 11. 2022 | Mgr. Jan Syřínek, v.r. ředitel školy

## Anotace

Cílem této ročníkové práce je za pomoci opensource programů navrhnout a z open-

source komponent poskládat robotické autíčko pro začátečníky i pokročilé s možností

jednoduchého sestavení. Dalším úkolem je vyvinout firmware a API pro jednoduché

skriptové programovaní i komplexnější programování s využitím obrazového vstupu.

Dalším úkolem je připravit ukázkové příklady kódu k předvedení jednotlivých funkcí

robota. Posledním úkolem je zpříjemnit práci s robotem, zhodnotit přínosy a možnosti

využití projektu ve vzdělávání a vypracovat potřebnou dokumentaci.

„Prohlašuji, že jsem tuto práci vypracoval samostatně a použil literárních pramenů

a informací, které cituji a uvadím v seznamu použité literatury a zdrojů informací.“

„Souhlasím s využitím mé práce učteli VOŠ a SPŠE Plzeň k výuce.“

Plzni dne: | Podpis: |

## Poděkování

Tímto bych chtěl poděkovat vedoucímu práce Jiřímu Švihlovi za pomoc s výběrem

komponent a obsahem dokumentace a rodině a přátelům za psychickou podporu. Také

děkuji všem dohromady za to, že mě k tomu včas dokopali.

## Obsah

Anotace | 2
Poděkování | 3
Obsah | 4
Úvod | 5
1 Cíle a požadavky | 6
2 Návrhový software | 7
3 Výrobní technologie | 11

4

## Úvod

V dnešní době se stále více hovoří o automatizaci a digitalizaci a tyto trendy mají

velký vliv na společnost. Robotika a autonomní systémy jsou jednou z klíčových oblastí,

které se rozvíjejí v rámci těchto trendů a mají potenciál změnit mnoho aspektů našeho

života.

Vzdělávání a výuka v této oblasti se také stávají stále důležitějšími, protože mnoho

pracovních pozic, které budou v budoucnosti vyžadovat znalosti robotiky a programo-

vání, ještě neexistuje. Výuka v této oblasti tak může být klíčová pro přípravu studentů

na pracovní trh budoucnosti.

Proto jsem se rozhodl věnovat svou ročníkovou práci právě problematice robotiky

a vytvořit autonomní auto, které bude sloužit jako výuková pomůcka. Můj záměr je

ukázat, jak moderní technologie mohou být využity k tomu, aby byly studenti lépe

připraveni na budoucí výzvy v oblasti robotiky a informatiky.

Při tvorbě prototypu se budu snažit využít nejnovější poznatky v oblasti robotiky a

programování, a to jak z teoretického hlediska, tak z praktického testování. Cílem bude

vytvořit zařízení, které bude snadno ovladatelné a srozumitelné pro studenty různých

věkových kategorií, a zároveň bude dostatečně funkční a výkonné pro splnění zadaných

úkolů.

Věřím, že tato ročníková práce přispěje k popularizaci robotiky a podpoří zájem

studentů o tuto oblast. Tím může mít pozitivní vliv na jejich budoucí kariéru a na

rozvoj robotiky v České republice.

5

## 1 Cíle a požadavky

### 1.1 Komponenty (moduly)

Hlavním cílem této ročníkové práce je návrh a výroba robota z běžně dostupných

materiálů, v tomto případě ze snadno sehnatelných modulů.

Moduly by měly být zároveň opensource, aby si software pro ně mohl programovat

každý, který se k robotovi dostane, nebo si ho sám vyrobí.

Důležitý je také výběr napájení, v případě robotického auta tedy baterie, tak, aby

udrželo robota v provozu po přiměřeně dlouhou dobu a aby zároveň dokázalo vykrýt

proudové špičky.

### 1.2 Šasi (tělo)

Tělo robota by mělo být vyrobeno tak, aby bylo plně uzavíratelné, tedy bezpečné

pro jakýkoli přenos i při nešetrném zacházení, ale aby se dal robot také provozovat

s plně přístupnými veškerými propojkami a bylo tedy snadné ladit jeho hardware za

provozu.

### 1.3 API

Jedním z dalších požadavků je co nejvíce zpříjemnit uživateli práci s robotickým

autem, tedy vytvořit nějaké API nebo knihovnu.

Nedílnou součástí je také dokumentace k danému API/knihovně a to proto, aby si i

nově příchozí uživatel zvládl bez jakékoli pomoci robota pomocí daného API/knihovny

naprogramovat.

6

## 2 Návrhový software

### 2.1 Onshape

Onshape je online software pro návrh 3D součástí. V programu se vytváří takzvaný

dokument, ve kterém se nadále dají zakládat „studia“. Onshape nabízí mnoho zajíma-

vých možností, typického uživatele však zajímají tato tři hlavní studia - Part Stuido,

Assembly a Drawing.

Part Studio

Part Studio slouží, jak už název napovídá, k vytváření jednotlivých dílů. Díly se

vytvářejí a upravují pomocí příkazů, jako například Sketch, sloužící k sestrojení 2D

náčrtu, Extrude, k „vytáhnutí“ náčrtu do třetího rozměru, nebo Fillet, k zaoblení

hran. Tyto příkazy lze vyvolat kliknutím na jejich ikonu v horní liště programu, přepsá-

ním jejich názvu do Search tools, nebo, u některých více používaných, klávesovými

zkratkami.


Obrázek 1: Part Studio

7

Assembly

Další studio v programu Onshape, Assmebly, slouží ke spojování (nebo alespoň aran-

žování) jednotlivých dílů. K tomuto účelu slouží příkazy, které se, opět, nechají vyvolat

několika způsoby, včetně klepnutím na ikonu v horní liště studia. Další výhodnou funkcí

tohoto studia je Create Part Studio in context, což dělá přesně to, co se v názvu

píše; vytvoří studio dílu v kontextu se sestavou. Tato funkce může hodně usnadnit

vytváření některých dílů.


Obrázek 2: Assembly

Drawing

Drawing se dá vyvolat jak samostatně, tak rovnou v kontextu s daným dílem a to

jak z Part Stuido, tak z Assembly. Uživateli stačí, kdy v seznamu dílů vybere danou

položku a přes kontextové menu vybere možnost Create Drawing of.... Výkres se

zde upravuje také pomocí příkazů, stejně jako v předešlých studiích. Drawing studio

umožňuje také globální nastavení kót, písma, čar atd.

8

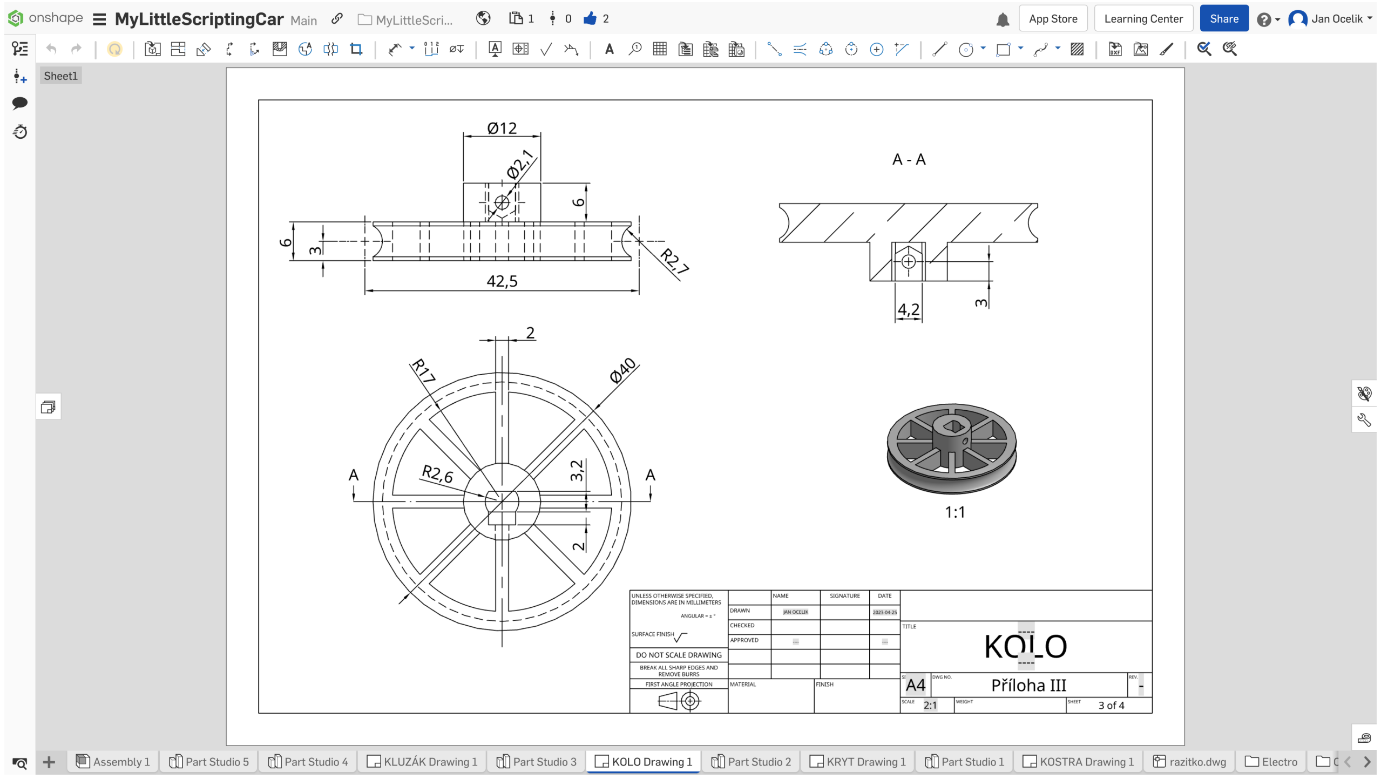
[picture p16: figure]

Obrázek 3: Drawing

### 2.2 Code OSS/VS Code

Code OSS je opensource IDE vyvíjené firmou Microsoft. Vzniklo jako konkurent

programu Atom, který nedávno rozválcoval. Stal se tak oblíbeným hlavně díky podpoře

obrovského množství programovacích i značkovacích jazyků (např. python, c++, java,

xml, html). Má také velice intuitivní ovládání a šikovně zvolenou paletu barev.

Code OSS a Vicual Studio Code jsou téměř identické programy, jediným pozorova-

telným rozdílem je absence některých rozšíření v „marketplace“ v Code OSS (i to se

dá ale snadno opravit).

9


Obrázek 4: Code OSS

PlatformIO

Platformio je rozšíření do VS Code umožňující překlad C++ kódu a následný upload

do předdefinovaných jednočipů (např. atmega328). Je to šikovný kus softwaru s několika

užitečnými funkcemi navíc, jako např. automatická detekce zařízení, seznam dostup-

ných knihoven, snadná instalace a integrace daných knihoven do projeků.

10

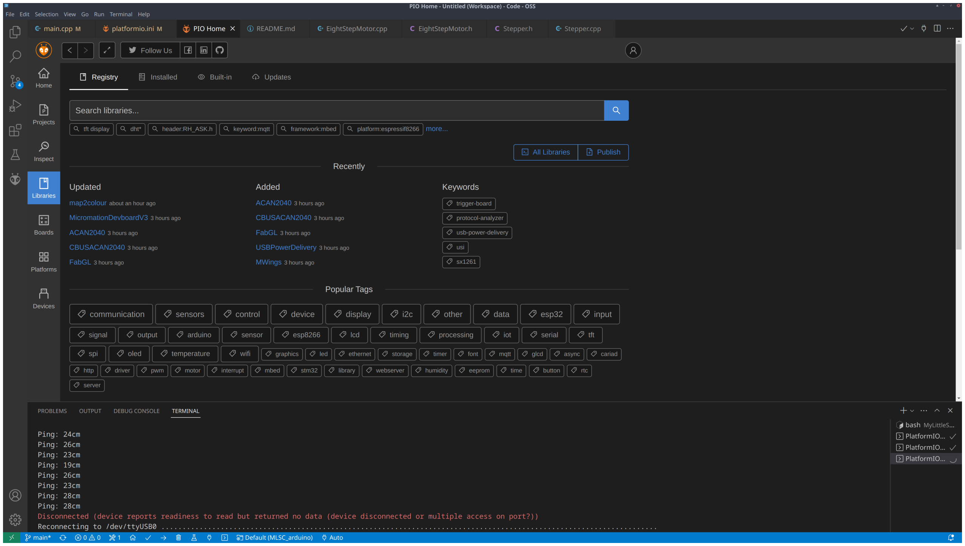
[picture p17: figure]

Obrázek 5: PlatformIO

11

## 3 Výrobní technologie

### 3.1 3D tisk

3D tisk je moderní technologie, která umožňuje vytvářet fyzické objekty ze 3D digitál-

ních modelů. Tento proces začíná vytvořením digitálního modelu pomocí počítačového

softwaru. Poté je tento digitální model převeden do formátu, který je kompatibilní s

3D tiskárnou. V průběhu tiskového procesu se materiál, obvykle termoplastického typu,

zahřívá a aplikuje na specifická místa v souladu s digitálním modelem. Tento postup

se opakuje vrstva po vrstvě, dokud není celý objekt hotov.

3D tisk má mnoho výhod. Například umožňuje rychlé prototypování a výrobu malých

sérií komplexních geometrických objektů. To se stává velmi užitečné v oblasti průmys-

lové výroby, kde může být vytvoření prototypu značně nákladné a časově náročné. Díky

3D tisku se náklady na výrobu mohou snížit a doba výroby může být zkrácena.

V posledních letech se cena 3D tiskáren snížila a uživatelé si mohou tisknout vlastní

návrhy přímo z domova. Tato technologie také umožňuje vytvářet přizpůsobené a je-

dinečné předměty, což je velmi užitečné pro řadu různých aplikací, včetně medicíny,

průmyslu a uměleckých oborů.

12

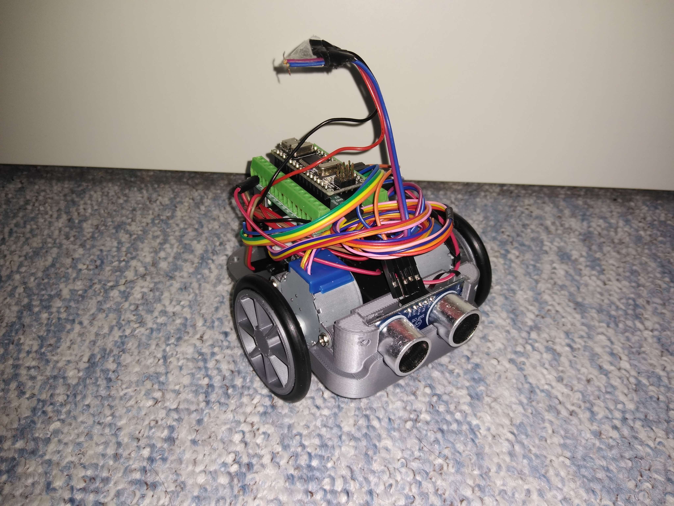
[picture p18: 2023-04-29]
docs/images/real_kostra.jpg

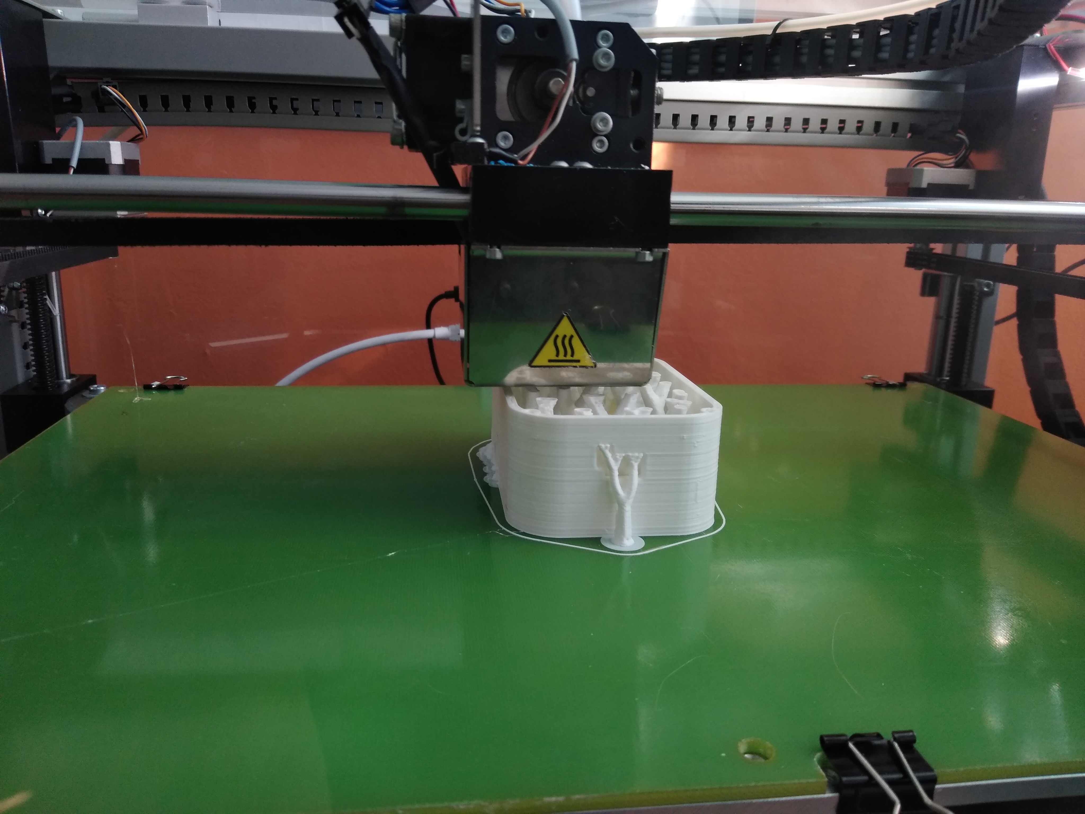
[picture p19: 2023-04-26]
docs/images/tisk_kryt.jpg

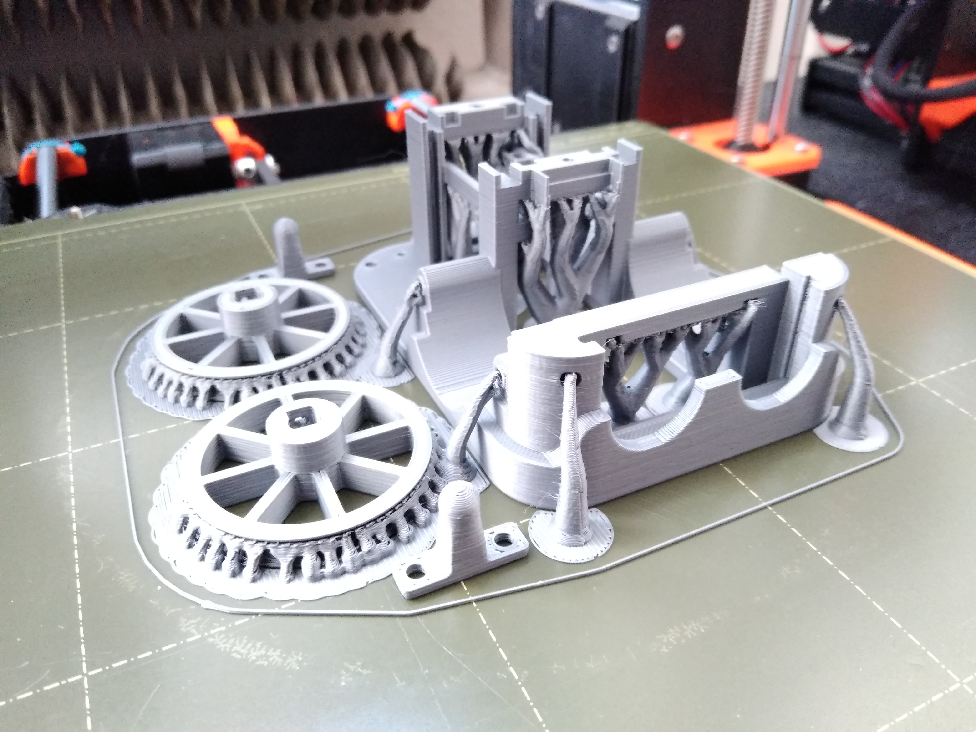
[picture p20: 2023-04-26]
docs/images/tisk_kostra.jpg

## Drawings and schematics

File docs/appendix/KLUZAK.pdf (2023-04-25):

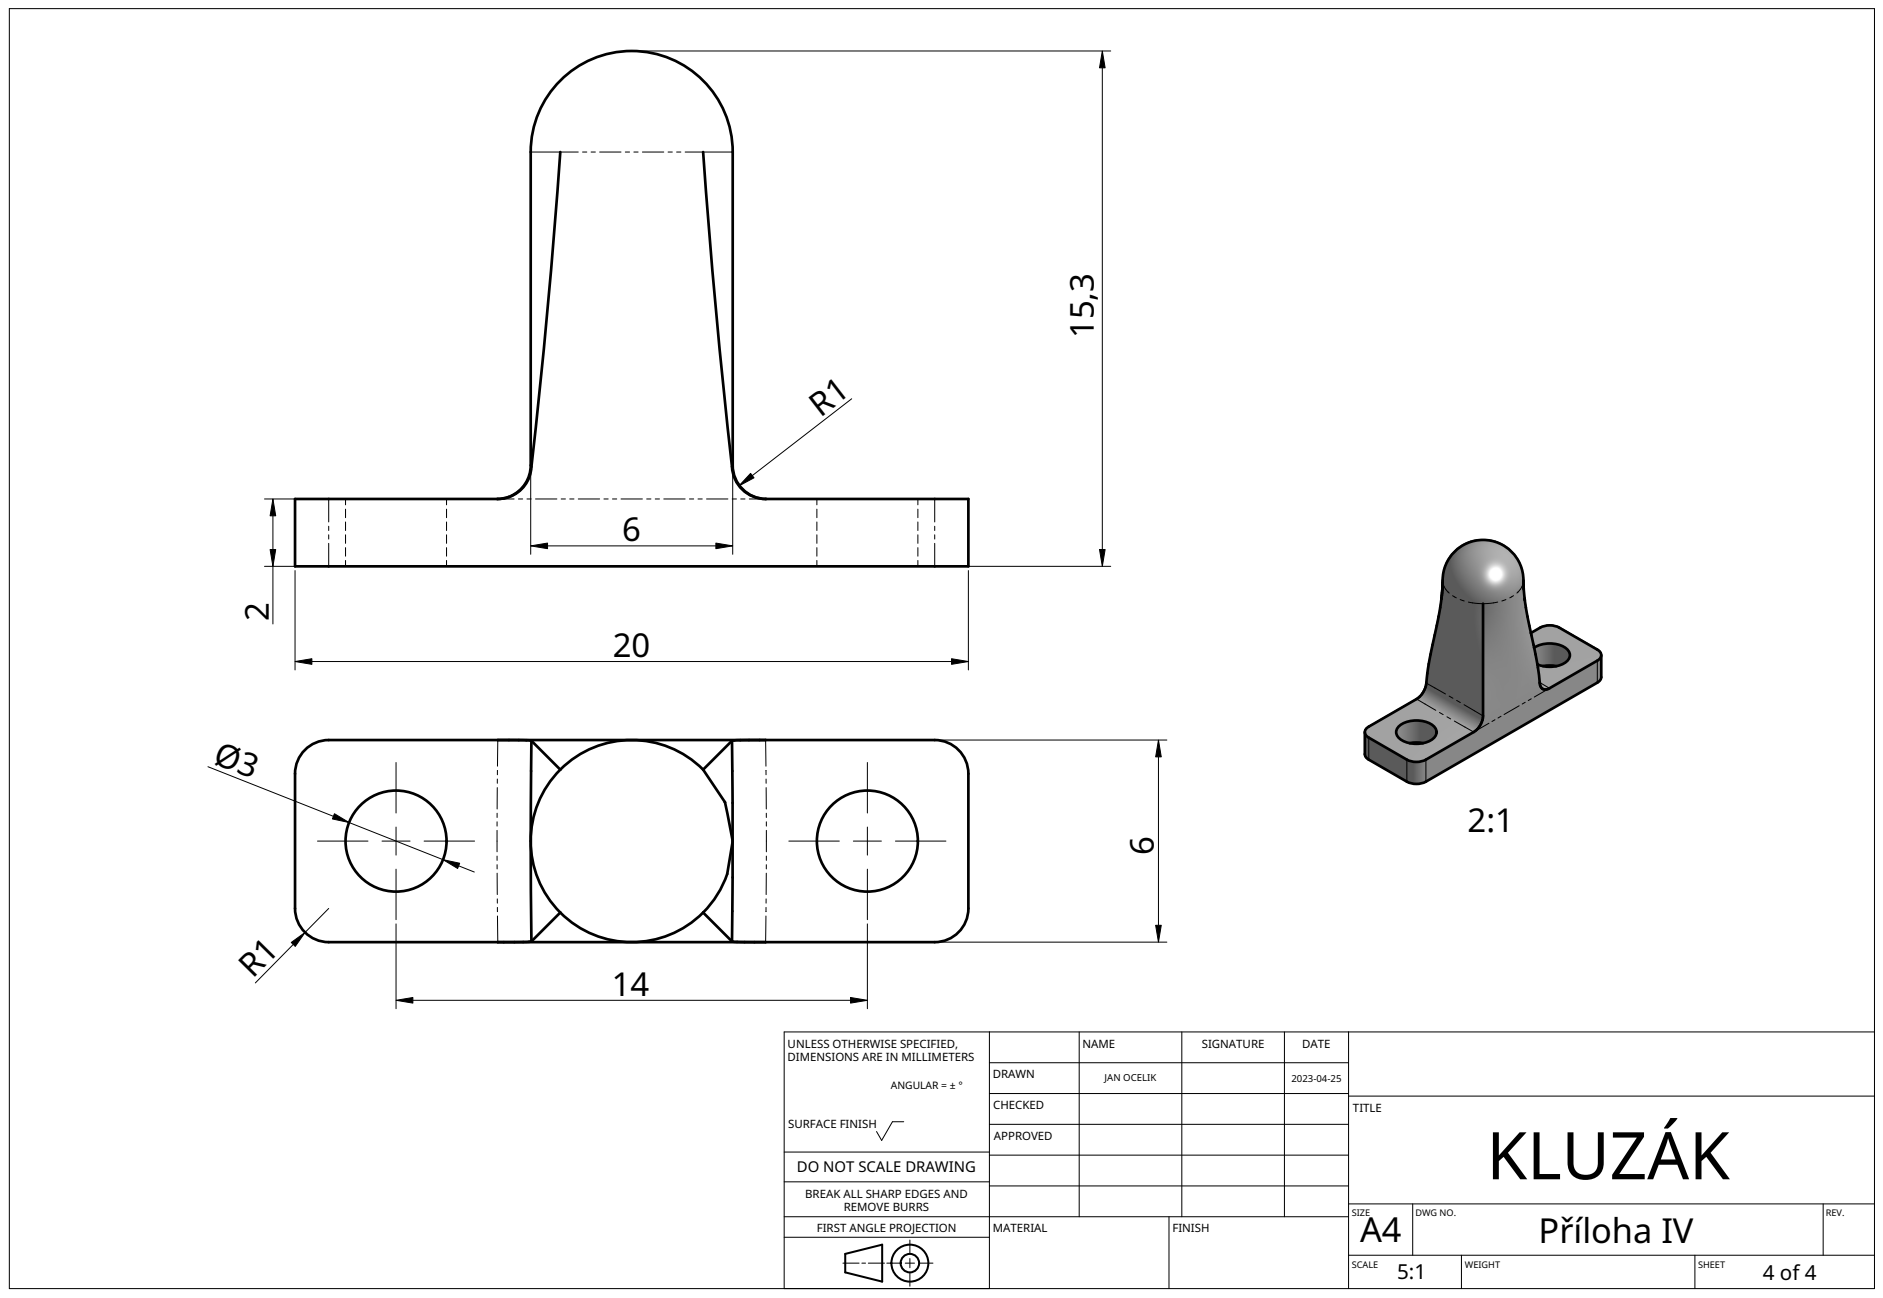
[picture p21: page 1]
MATERIAL; FINISH

UNLESS OTHERWISE SPECIFIED, DIMENSIONS ARE IN MILLIMETERS ANGULAR = ± ° SURFACE FINISH | | NAME | SIGNATURE | DATE

DRAWN | JAN OCELIK | | 2023-04-25

CHECKED | | | | TITLE KLUZÁK SIZE

APPROVED

DO NOT SCALE DRAWING

BREAK ALL SHARP EDGES AND

REMOVE BURRS
FIRST ANGLE PROJECTION

A4 | DWG NO. Píloha IV | REV.

SCALE 5:1 | WEIGHT | SHEET 4 of 4

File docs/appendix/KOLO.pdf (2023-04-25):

A - A

Ø12

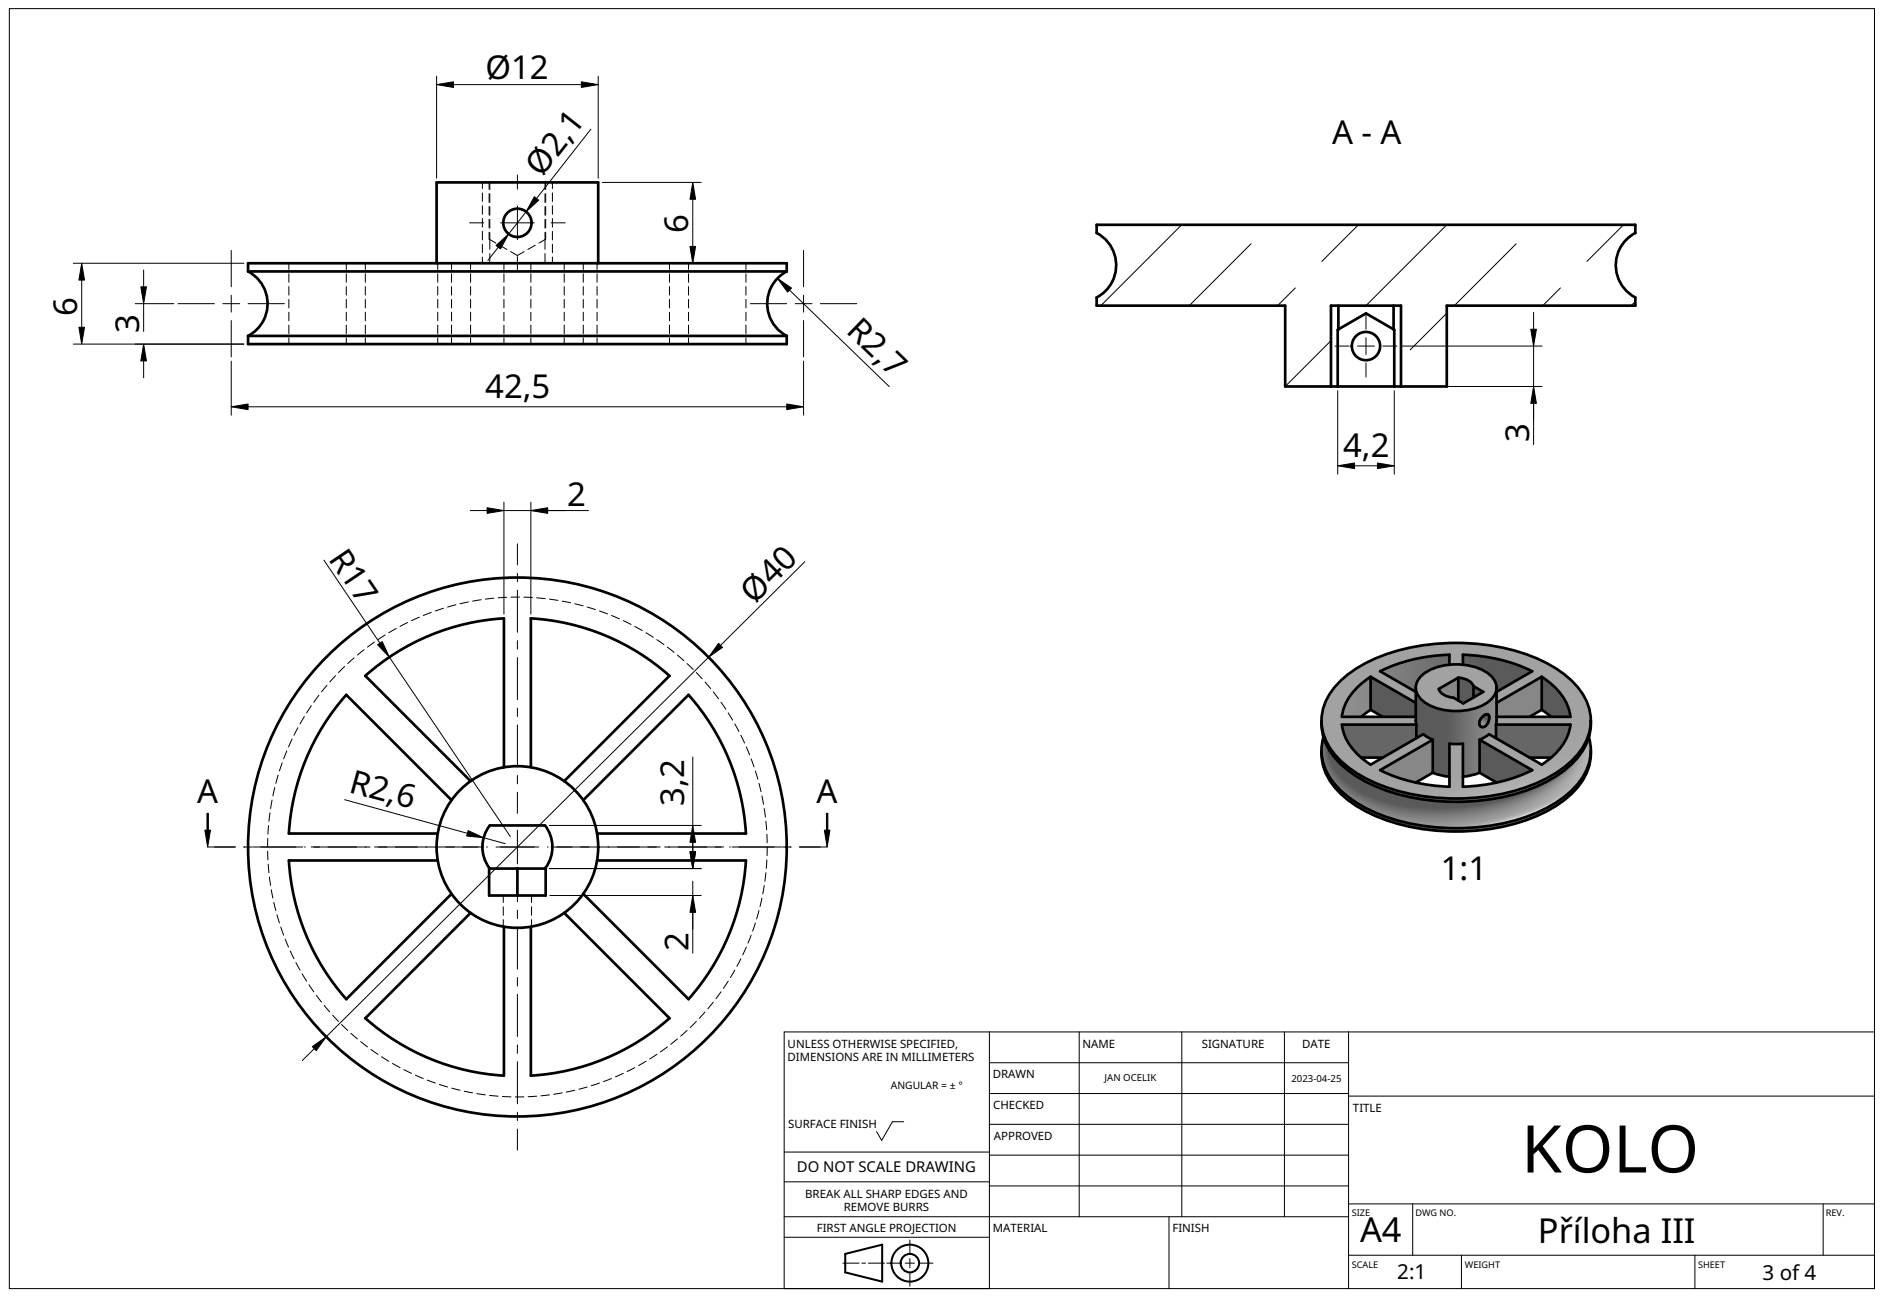
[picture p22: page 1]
MATERIAL; FINISH

UNLESS OTHERWISE SPECIFIED, DIMENSIONS ARE IN MILLIMETERS ANGULAR = ± ° SURFACE FINISH | | NAME | SIGNATURE | DATE

DRAWN | JAN OCELIK | | 2023-04-25

CHECKED | | | | TITLE KOLO SIZE

APPROVED

DO NOT SCALE DRAWING

BREAK ALL SHARP EDGES AND

REMOVE BURRS
FIRST ANGLE PROJECTION

A4 | DWG NO. Píloha III | REV.

SCALE 2:1 | WEIGHT | SHEET 3 of 4

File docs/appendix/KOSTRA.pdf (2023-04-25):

A

A - A

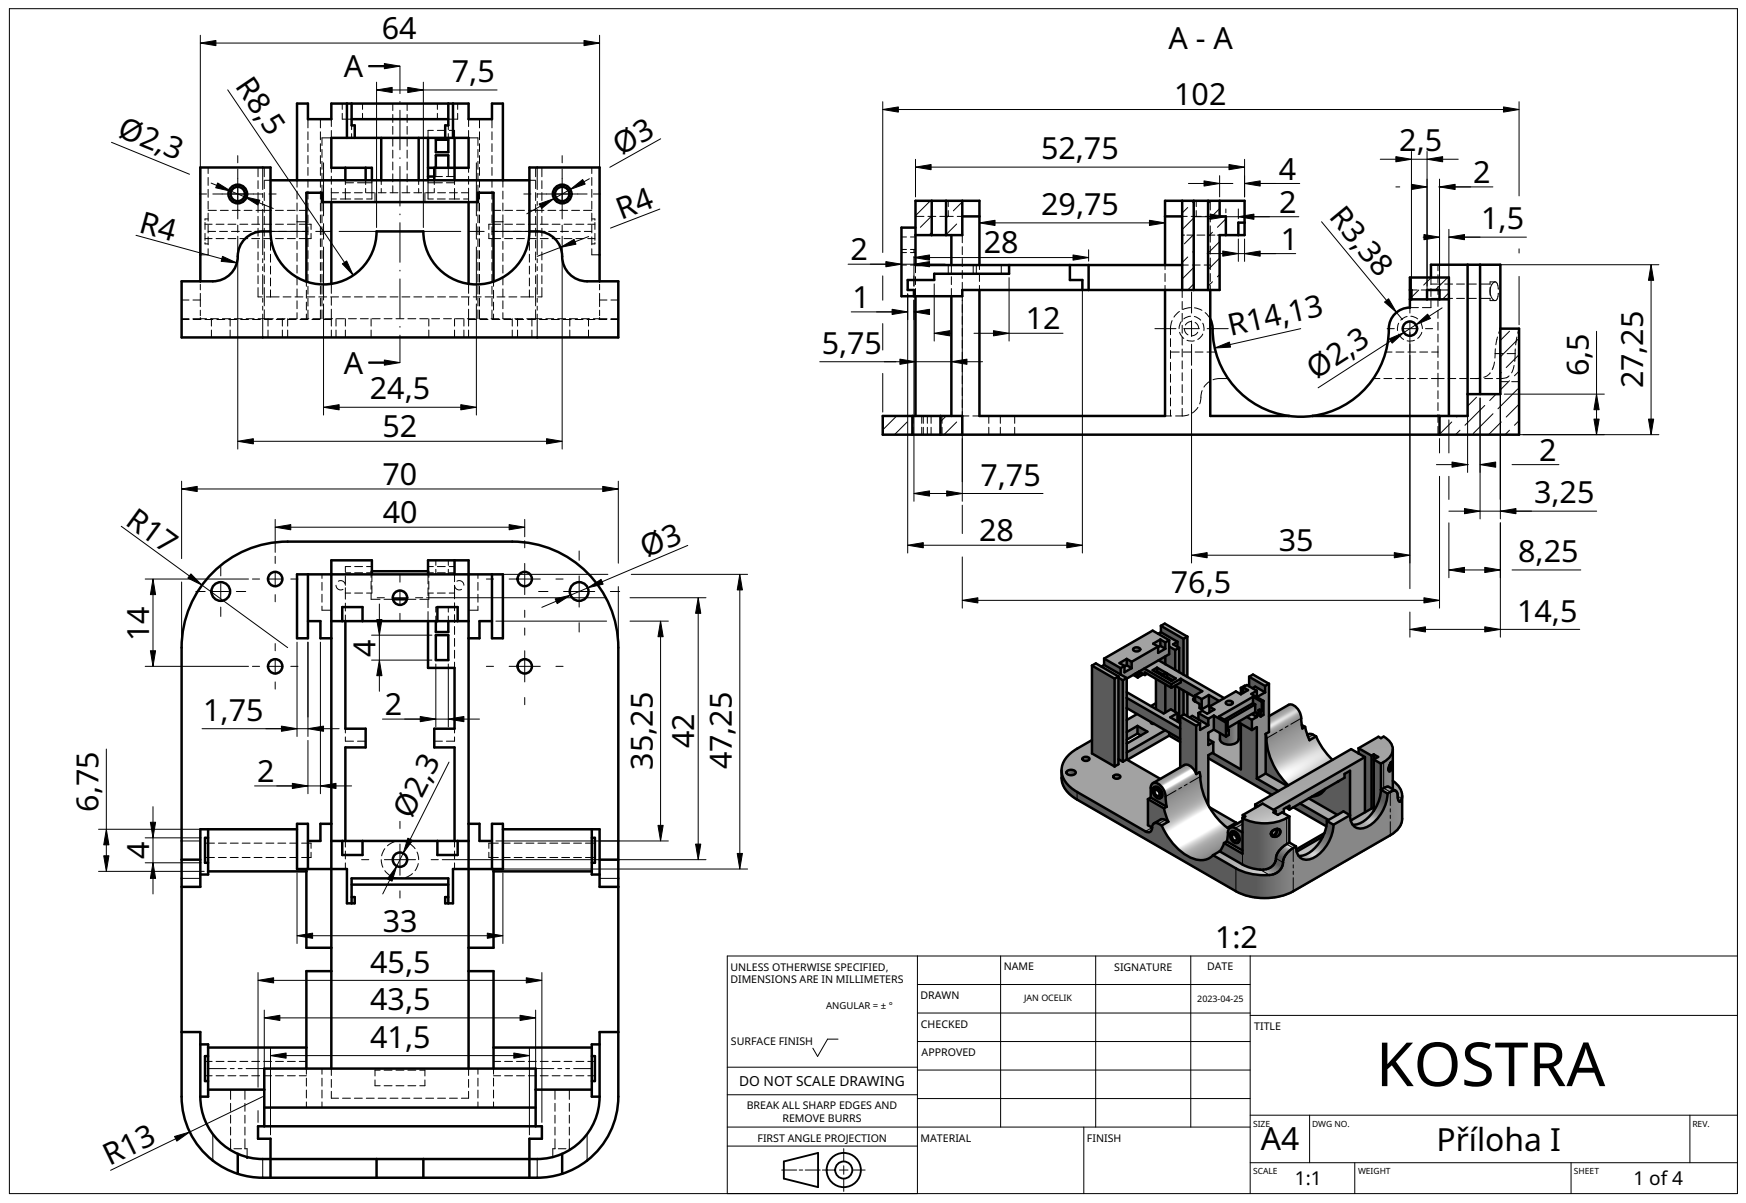
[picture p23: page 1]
ANGULAR = ± °; SURFACE FINISH; NAME; SIGNATURE; DATE; DRAWN; JAN OCELIK; CHECKED; APPROVED; MATERIAL; FINISH; TITLE KOSTRA SIZE

UNLESS OTHERWISE SPECIFIED,
DIMENSIONS ARE IN MILLIMETERS

DO NOT SCALE DRAWING

BREAK ALL SHARP EDGES AND

REMOVE BURRS
FIRST ANGLE PROJECTION

A4 | DWG NO. Píloha I | REV.

SCALE 1:1 | WEIGHT | SHEET 1 of 4

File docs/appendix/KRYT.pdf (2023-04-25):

28

21 | 1 R13

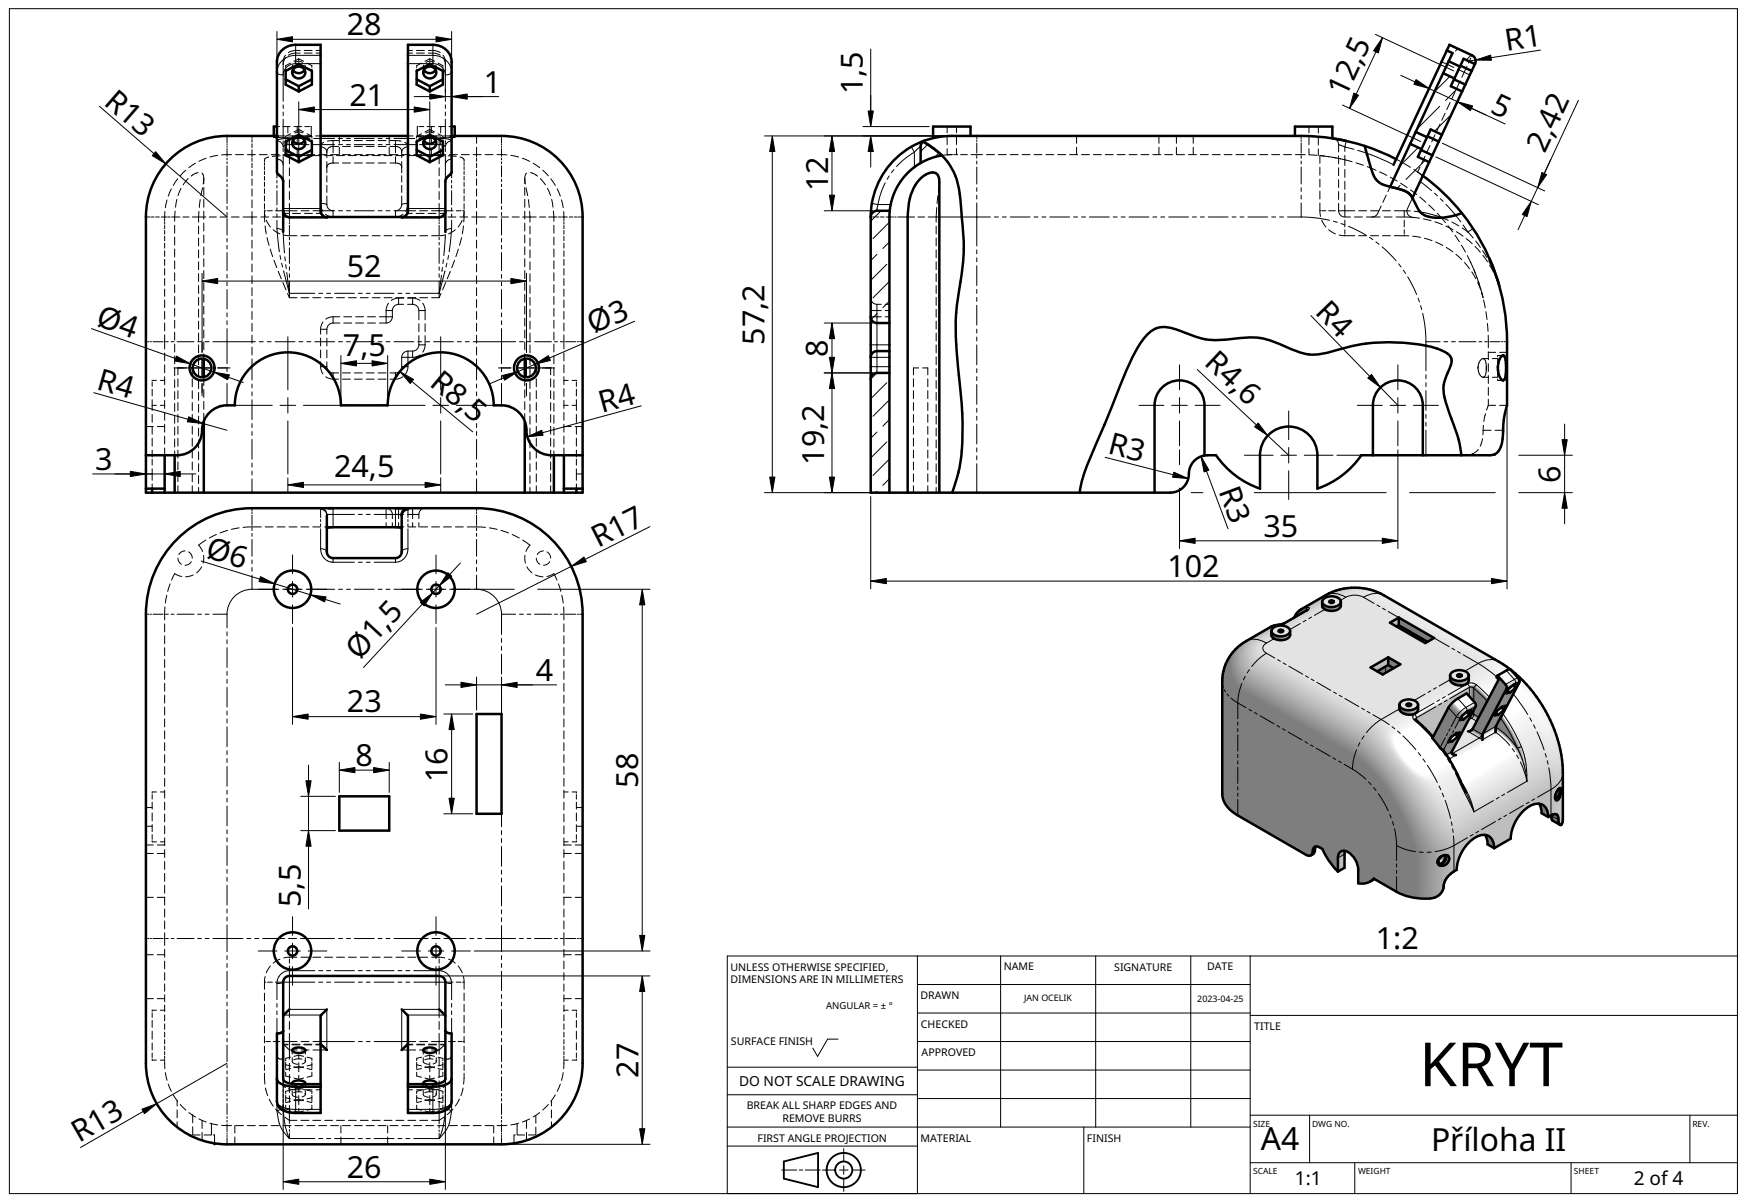
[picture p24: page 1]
MATERIAL; FINISH

UNLESS OTHERWISE SPECIFIED, DIMENSIONS ARE IN MILLIMETERS ANGULAR = ± ° SURFACE FINISH | | NAME | SIGNATURE | DATE

DRAWN | JAN OCELIK | | 2023-04-25

CHECKED | | | | TITLE KRYT SIZE

APPROVED

DO NOT SCALE DRAWING

BREAK ALL SHARP EDGES AND

REMOVE BURRS
FIRST ANGLE PROJECTION

A4 | DWG NO. Píloha II | REV.

SCALE 1:1 | WEIGHT | SHEET 2 of 4

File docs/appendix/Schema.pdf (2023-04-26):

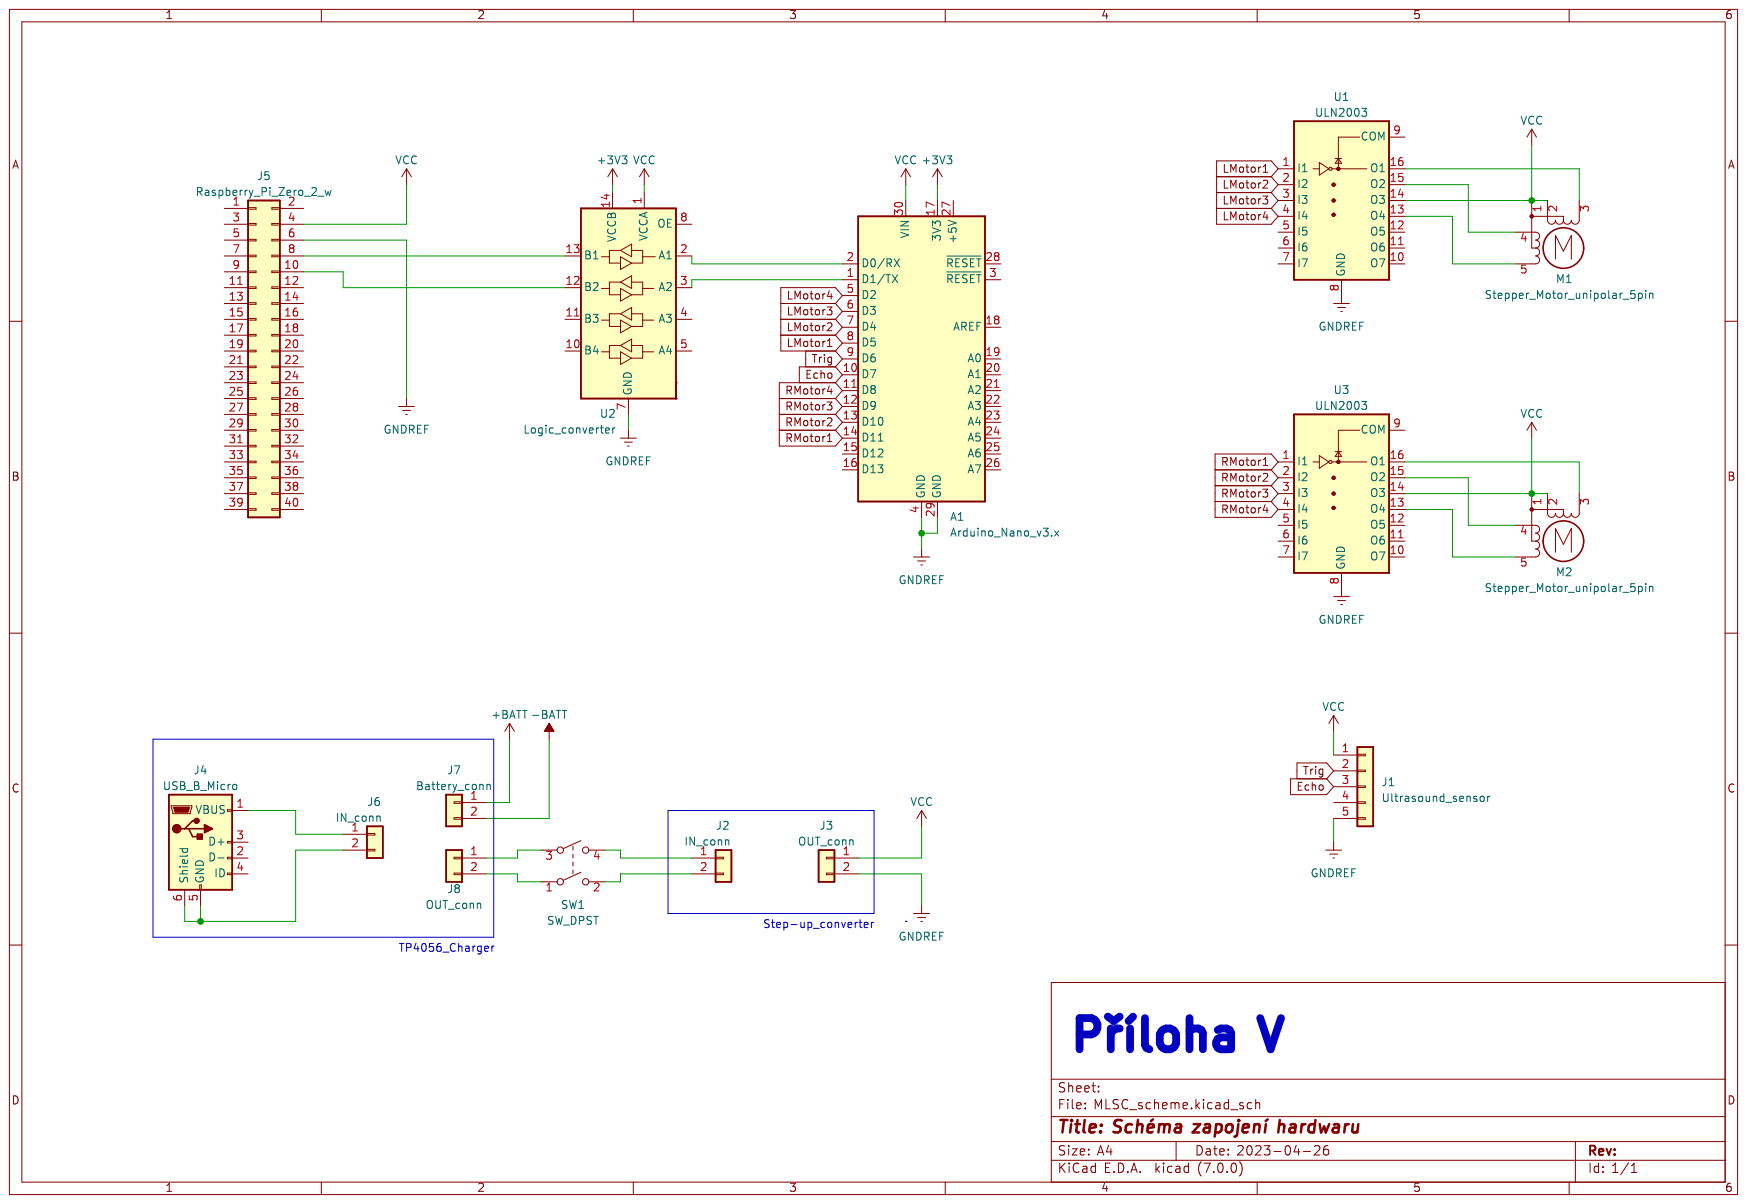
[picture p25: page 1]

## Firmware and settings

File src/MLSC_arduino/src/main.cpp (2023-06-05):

#include <Arduino.h>
#include <EightStepMotor.h>
#include <NewPing.h>

#define PINCOUNT 4
#define STEPS 8
#define REVOLUTION 4096

#define TRIGGER_PIN  6   // Arduino pin tied to trigger pin on ping sensor.
#define ECHO_PIN     7   // Arduino pin tied to echo pin on ping sensor.
#define MAX_DISTANCE 200 // Maximum distance we want to ping for (in centimeters). Maximum sensor distance is rated at 400-500cm.

float rpm = -15;
int timer_us = 60*1000L*1000L/REVOLUTION/rpm;
int lpins[PINCOUNT] = {8, 9, 10, 11};
int rpins[PINCOUNT] = {2, 3,  4,  5};

// Variables for Serial communication:
String command = ""; 

// Variables for ultrasonic sensor:
unsigned long last;
bool ping_on = 0;
unsigned int last_dist = 0;  // Variable for saving the ultrasonic measurements
unsigned int pingSpeed = 50; // How frequently are we going to send out a ping (in milliseconds). 50ms would be 20 times a second.
unsigned long pingTimer;     // Holds the next ping time.

EightStepMotor *m;
EightStepMotor LMotor(REVOLUTION, lpins[3], lpins[2], lpins[1], lpins[0]);
EightStepMotor RMotor(REVOLUTION, rpins[3], rpins[2], rpins[1], rpins[0]);

NewPing sonar(TRIGGER_PIN, ECHO_PIN, MAX_DISTANCE); // NewPing setup of pins and maximum distance.

void echoCheck() { // Timer2 interrupt calls this function every 24uS where you can check the ping status.
  if (sonar.check_timer()) { // Checks to see if the ping was received.
    last_dist = (sonar.ping_result / US_ROUNDTRIP_CM); // Ping returned, uS result in ping_result, convert to cm with US_ROUNDTRIP_CM.
  }
}

void doCommand(String command) {
  // determine the device we want to use:
  switch (command[1])
  {
  case 'r':
    m = &RMotor;
    break;
  
  case 'l':
    m = &LMotor;
    break;
  
  case 'u':  // Whole code for ultrasonic sensor:
    if (command[0] == 'g') {
      Serial.print("u");
      Serial.println(last_dist);
    }
    else if (command[0] == 's') { ping_on = command[2]-'0'; }
    return;
    
  default:
    return;
  }

  // Code for controling/reading motor values:
  if (command[0] == 'g') {
    if (command[2] == 'v') {
      Serial.print(command[1]);
      Serial.print("v");
      Serial.println(m->getRPM());
    }
    else if (command[2] == 'n') {
      Serial.print(command[1]);
      Serial.print("n");
      Serial.println(m->getSteps());
    }
  }
  else if (command[0] == 's') {
    if (command[2] == 'v') { m->setRPM(command.substring(3).toInt()); }
    else if (command[2] == 'n') { m->setSteps(command.substring(3).toInt()); }
  }
}

void doSerial() {
  if (Serial.available() > 0) {
    char incomingChar = Serial.read();
    
    // If the string is complete, run this:
    if (incomingChar == '\n') {
      // Serial.print("Received string: ");
      // Serial.println(command);
      doCommand(command);
      command = "";
      return;
    }
    
    // Add the character to the input string
    command += incomingChar; 
  }
}

void setup() {
  // put your setup code here, to run once:
  for (int i=0; i<PINCOUNT; i++) {
    pinMode(lpins[i], OUTPUT);
  }
  for (int i=0; i<PINCOUNT; i++) {
    pinMode(rpins[i], OUTPUT);
  }

  command.reserve(64);
  command = "";

  last = millis();
  pingTimer = millis(); // Start now.
  Serial.begin(115200);
}

void loop() {
  // put your main code here, to run repeatedly:
  doSerial();

  if (LMotor.tick()) Serial.println("ln0");
  if (RMotor.tick()) Serial.println("rn0");

  // Notice how there's no delays in this sketch to allow you to do other processing in-line while doing distance pings.
  if ((millis() >= pingTimer) && ping_on) {   // pingSpeed milliseconds since last ping, do another ping.
    pingTimer += pingSpeed;      // Set the next ping time.
    sonar.ping_timer(echoCheck); // Send out the ping, calls "echoCheck" function every 24uS where you can check the ping status.
  }
}

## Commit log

2022-11-09 Added 3d model
    [car_model.FCStd]
2023-03-15 Changed continuous servos for stepper motors
2023-04-25 BIG and FAT update
    [car_model.FCStd]
2023-04-26 Another big update
    [MLSC_scheme.kicad_pcb, MLSC_scheme.kicad_sch]
